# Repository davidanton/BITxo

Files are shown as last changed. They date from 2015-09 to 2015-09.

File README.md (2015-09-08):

# BITxo

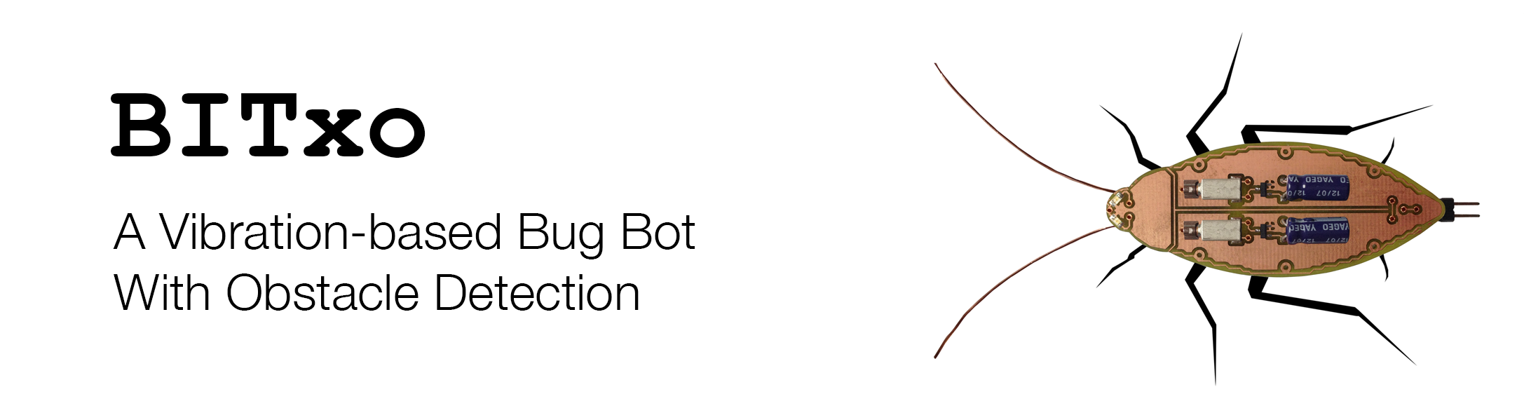
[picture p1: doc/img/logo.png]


---
###Stage of the project: **Prototyping**
---

####System Description

BITxo (pronounced */ˈbiʧo/*, Spanish for *bug*) is a bug bot that is able to move thanks to two ERM (eccentric rotating mass) vibration motors placed on the PCB. The centripetal force generated by the eccentric rotating mass is transmitted along the X and Z axes, being the Y axis the one collinear with the axis of rotation and the Z axis parallel to the normal of the PCB. The motors on BITxo rotate in opposite directions, canceling out the forces generated by both ERM vibration motors along the X axes and thus creating and up-down motion that would allow BITxo to move forward. Two single-core copper wires, attached each to a mechanical endstop, serve as BITxo's antennas. When one of the endstops is pressed against an obstacle, one of the ERM vibration motors stops rotating, therefore BITxo would rotate in the opposite direction of the obstacle.

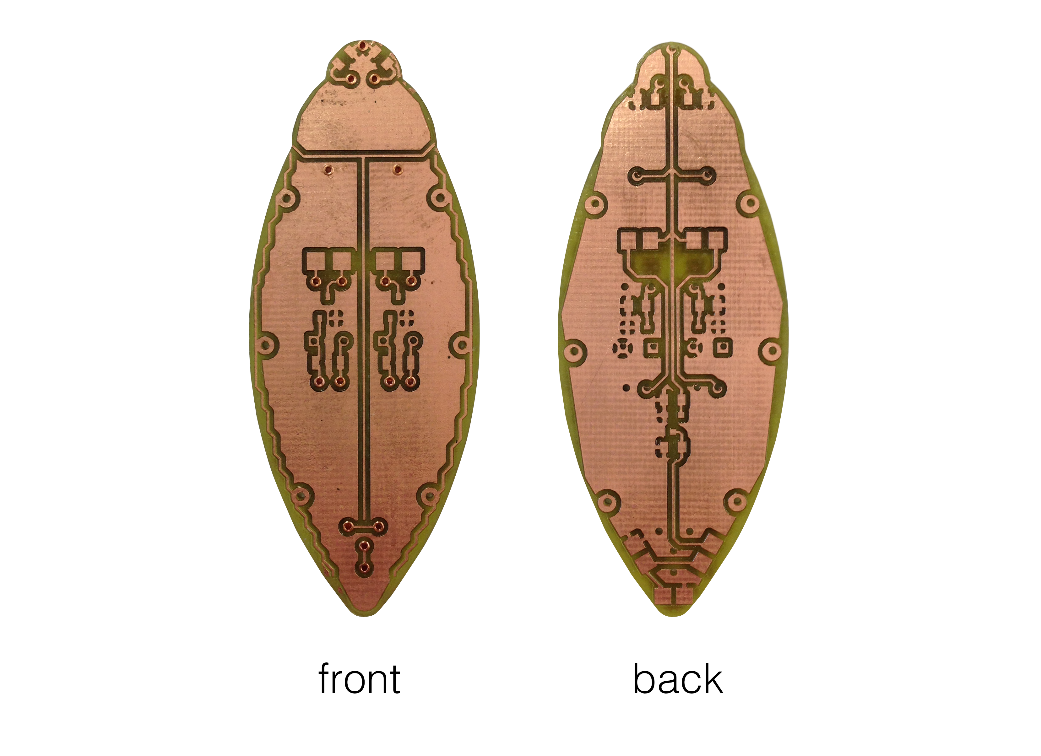
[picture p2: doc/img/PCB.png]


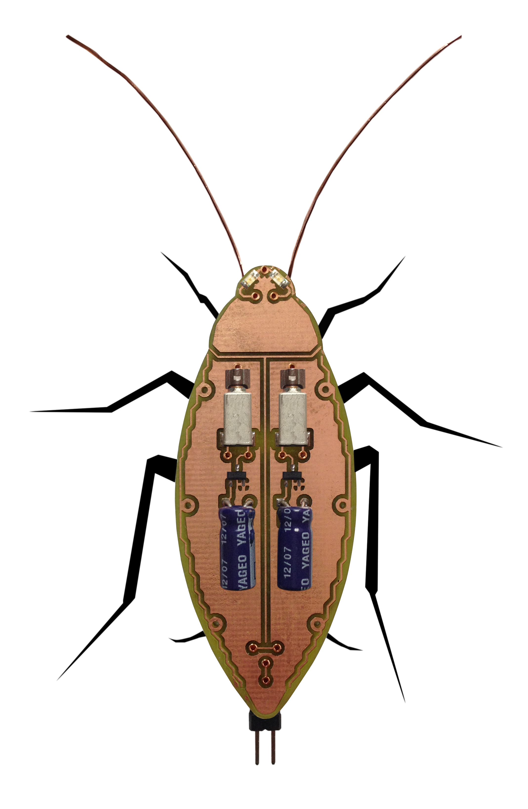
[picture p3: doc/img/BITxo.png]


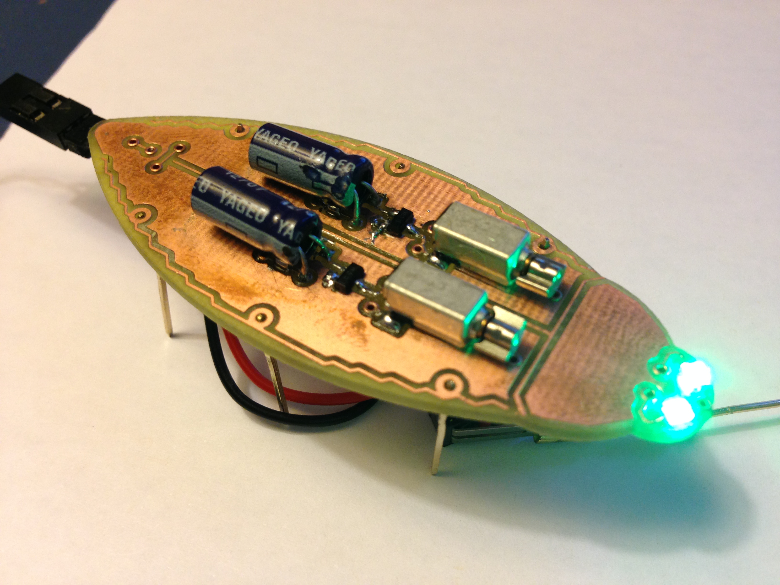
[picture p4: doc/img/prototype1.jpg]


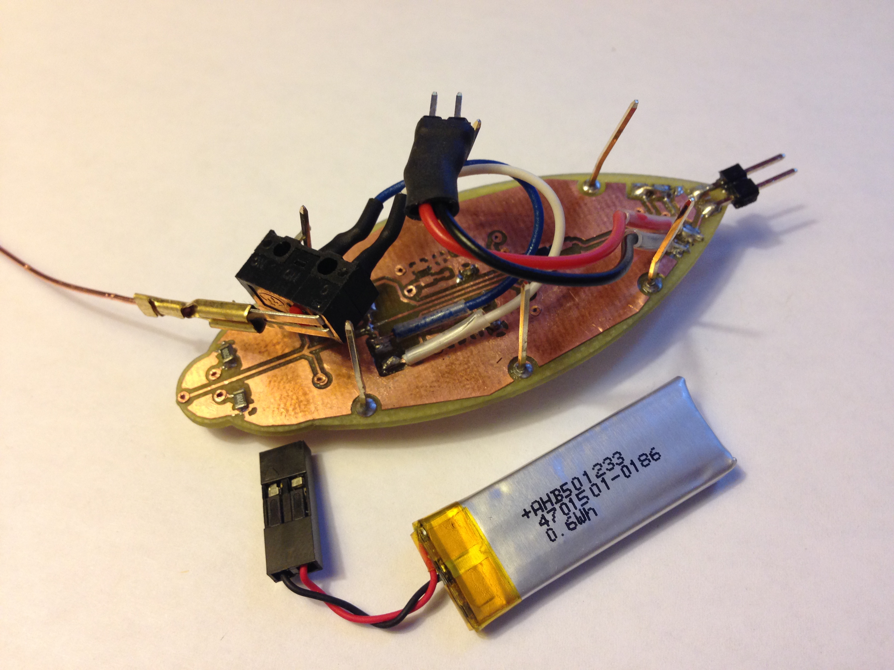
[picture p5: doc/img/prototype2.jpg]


####Principle of Operation

The voltage is regulated by a linear regulator to 3.3V, the maximum operating voltage of the ERM vibration motors. The time during which the ERM vibration motor stops rotating depends on the RC time constant of *R1* and *C3* as shown in the figure. When the endstop is pressed, the capacitor *C3* charges and the ERM vibration motor *M1* stops vibrating. When the endstop is released, the capacitor would discharge and when its voltage reaches a certain threshold, the p-MOSFET *Q1* would allow *M1* to vibrate again.

The filtering capacitor *C4* and the flyback diode *D1* are not necessary for this simple design, but may be used in future implementations.

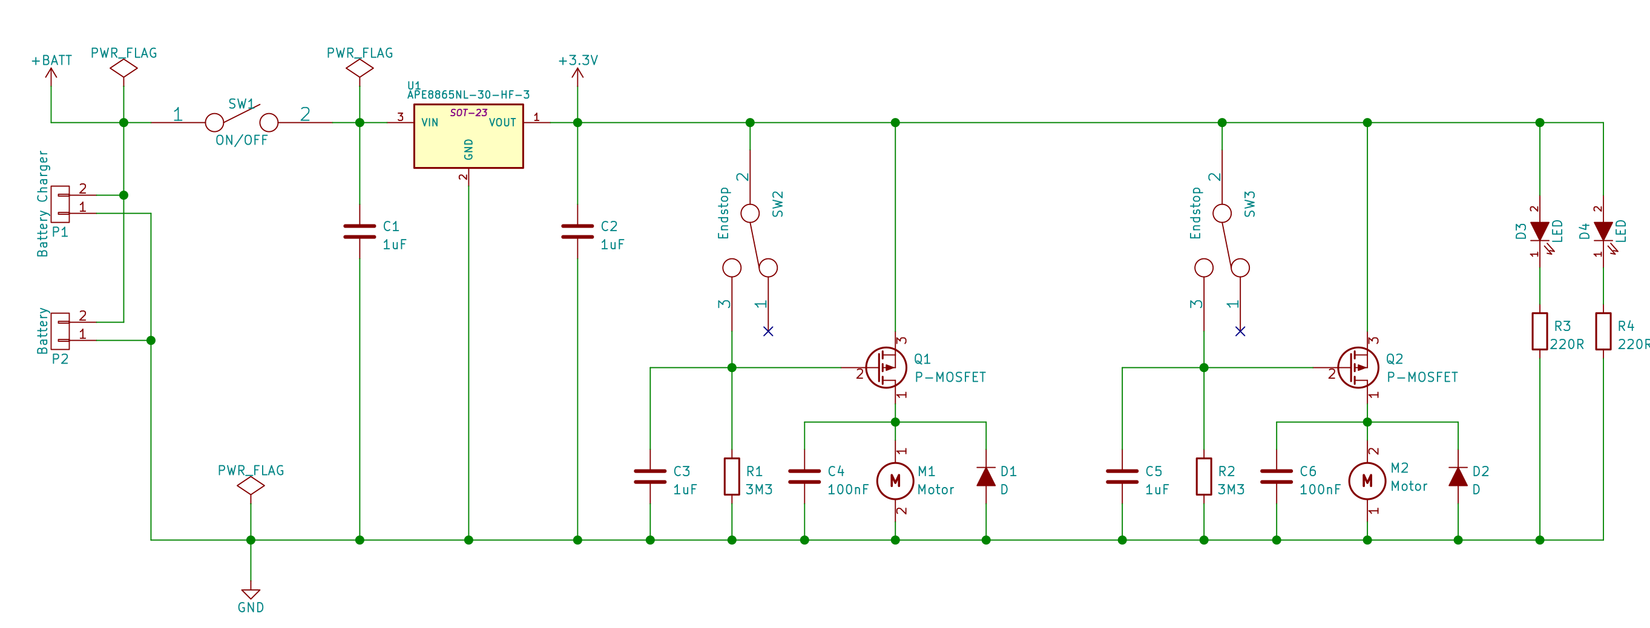
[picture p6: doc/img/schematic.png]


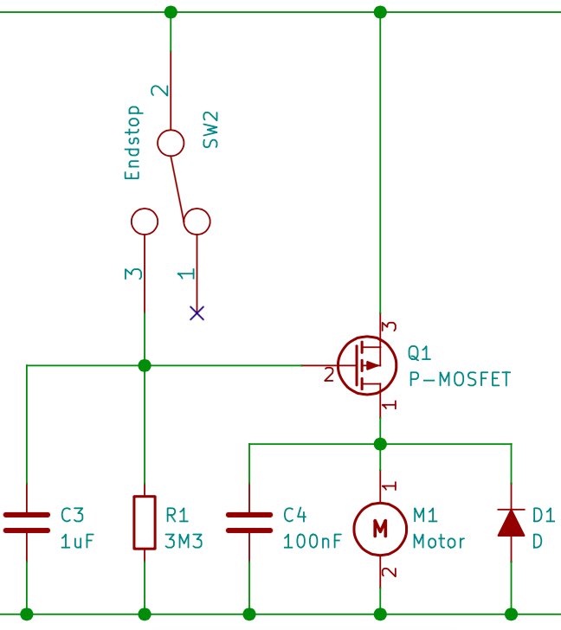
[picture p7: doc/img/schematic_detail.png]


Initial tests show that calibration is crucial for a stable forward motion. The pins used as legs don't function very well in that regard. A suggestion small slanted brushes, adding homogeneity, stability and allowing forward motion due to their slanted bristle position.

The performance of the capacitor circuit is not as reliable as first thought. An implementation using a microcontroller such as an ATtiny would be the next step in the design process.

####Video

https://www.youtube.com/watch?v=kGmnQzfZgtA

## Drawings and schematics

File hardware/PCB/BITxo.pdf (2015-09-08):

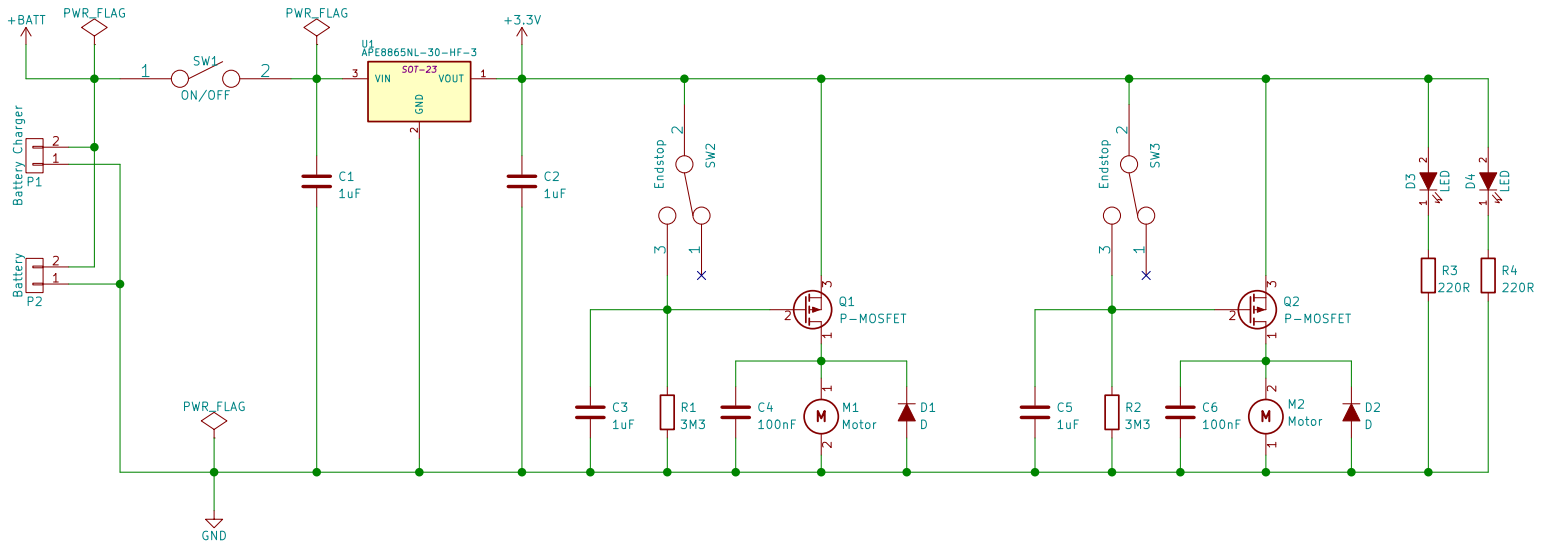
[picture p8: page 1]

Id: 1/1 Title: File: BITxo.sch Sheet: /

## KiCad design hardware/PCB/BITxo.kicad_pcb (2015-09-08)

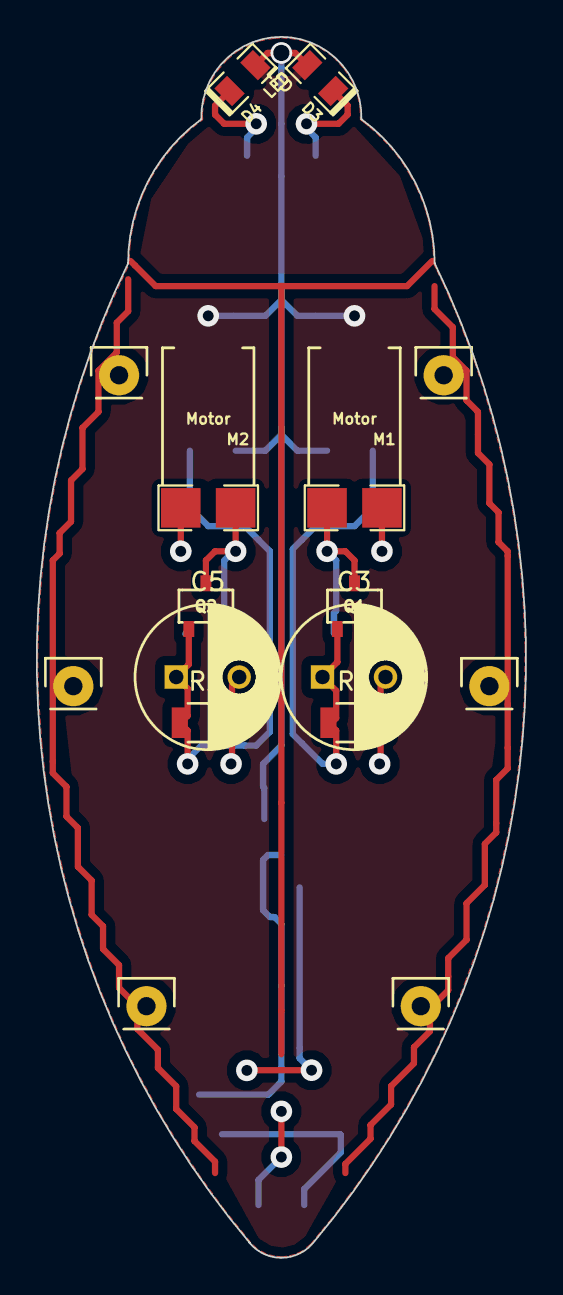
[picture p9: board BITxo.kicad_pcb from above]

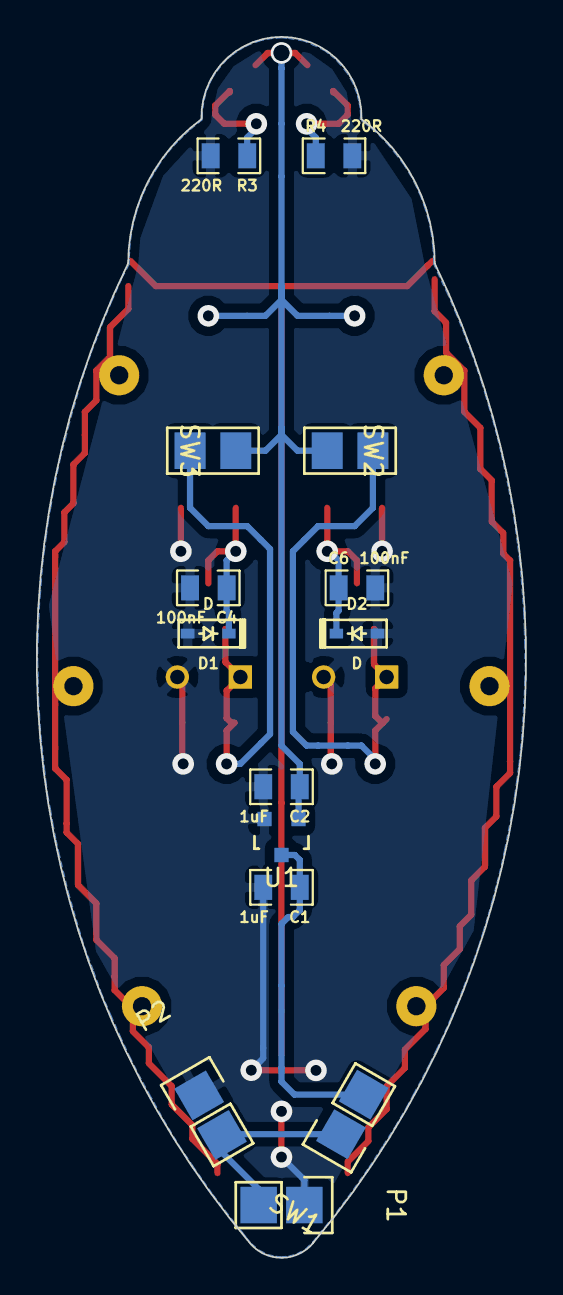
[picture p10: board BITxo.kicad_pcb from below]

Board: 2 copper layers, 27.2 x 67.8 mm, 24 parts (14 on the bottom side), 10 nets.

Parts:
C1, C2: 1uF; SMD0805
C3, C5: 1uF; C_Radial_D8_L11.5_P3.5
C4, C6: 100nF; SMD0805
D1, D2: D; SOD-323
D3, D4: LED; SMD0805_LED
M1, M2: Motor; Vibration_motor
P1: Battery Charger; Pads_1x02
P2: Battery; Pads_1x02
Q1, Q2: P-MOSFET; SOT23-5_MOD_PINOUT
R1, R2: 3M3; R_1206
R3, R4: 220R; SMD0805
SW1: ON/OFF; Pads_1x02
SW2, SW3: Endstop; Pads_Endstop
U1: APE8865NL-30-HF-3; SOT-23

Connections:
+3V3: C2.1, D3.2, D4.2, Q1.3, Q2.3, SW2.2, SW3.2, U1.1
+BATT: P1.2, P2.2, SW1.1
GND: C1.2, C2.2, C3.2, C4.2, C5.2, C6.2, D1.2, D2.2, M1.2, M2.1, P1.1, P2.1, R1.2, R2.2, R3.2, R4.2, U1.2
unnamed: C1.1, SW1.2, U1.3
unnamed: C3.1, Q1.2, R1.1, SW2.3
unnamed: C4.1, D1.1, M1.1, Q1.1
unnamed: C5.1, Q2.2, R2.1, SW3.3
unnamed: C6.1, D2.1, M2.2, Q2.1
unnamed: D3.1, R3.1
unnamed: D4.1, R4.1

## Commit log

2015-09-08 Add PCB
    [BITxo.kicad_pcb, BITxo.sch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]
2015-09-08 Add schematic
2015-09-08 Add schematic images for documentation
